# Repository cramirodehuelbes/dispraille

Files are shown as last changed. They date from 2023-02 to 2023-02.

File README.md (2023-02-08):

# Dispraille
For MakeHarvard 2023, we wanted to challenge ourselves by making a project centered around a braille display.

Dispraille is a module that uses optical character recognition (OCR) software to detect text around its user and convert it to braille using a 6-pin tactile interface. By placing a finger on the 3x2 matrix on the top of Dispraille, users can choose to read the text around them through a quick letter-by-letter run-through. For extra challenge, we chose to limit ourselves in making this project with only the materials that MakeHarvard provided, leading us to both enter in and win the top prize in the MakeHarvard Original category.

## Mechanical System
Our mechanical system used a rack and pinion mechanism to lift the pins out of the display. Since braille is very size-specific, we added bent pins in order to bypass the limitation of the larger servo motors and make the display regulation braille size with six micro-servos. We then mounted these into a custom 3D printed case and cover.

## Software
Our software system uses the OpenCV and Tesseract Python libraries in order to create a real-time optical character recognition (OCR) system. This reads text from a webcam live feed and sends serial information to an Arduino sketch, which converts the text into servo commands and lifts the corresponding pins. 

## Electrical
Our electrical subsystem is made up of an Arduino module which is connected to a Raspberry Pi through USB and our set of six motors through its six digital pins. Each pin is mapped to a different position on the braille display, and each letter is mapped to a different combination of pins according to Braille 1. Our electrical subsystem also includes a vibrating motor and a button. The vibrating motor is to alert the user that the webcam is recognizing text, while the button confirms that the user would like the text to be translated to braille.

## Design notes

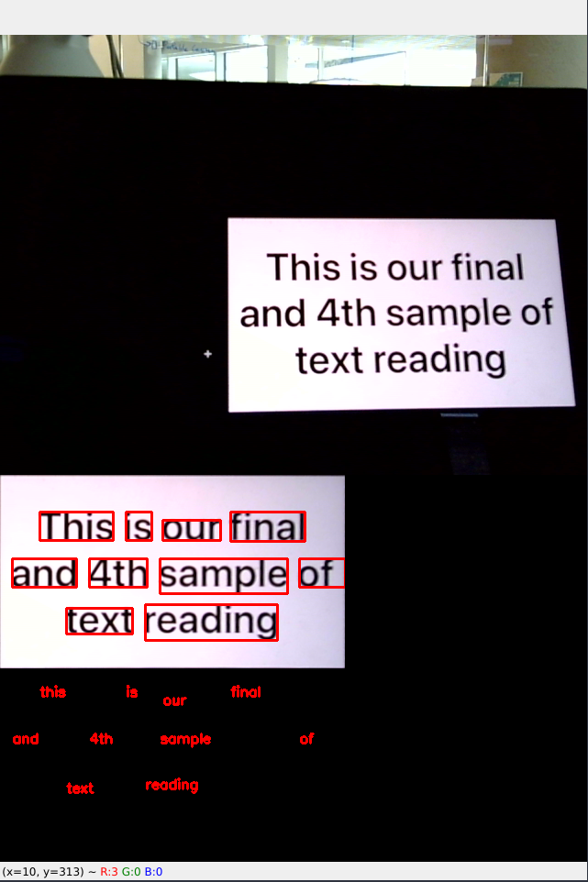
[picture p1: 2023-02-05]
vis_ss.png

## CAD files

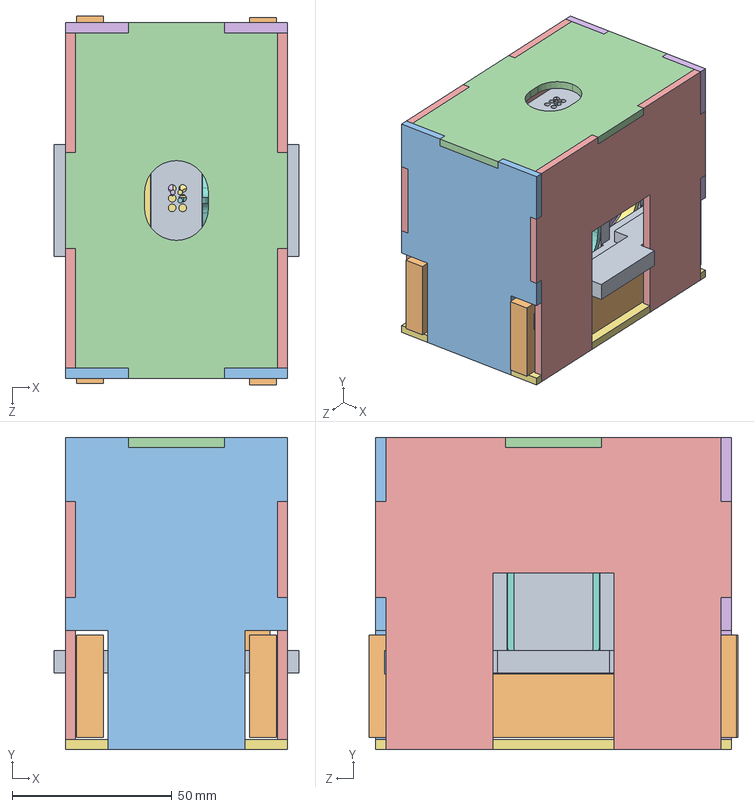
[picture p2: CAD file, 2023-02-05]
cad/Sprint 2 - x6/x6Assembly.SLDASM
76.6 x 97.7 x 115.4 mm
SixBasePart
ServoMotor
spur gear_am
rack spur rectangular_am
loop
loopArmA
loopArmB
loopArmC
Top Cover
Feet x 2
BoxBackFront
BoxRoof
BoxSides x 2
BoxBack
Box Base

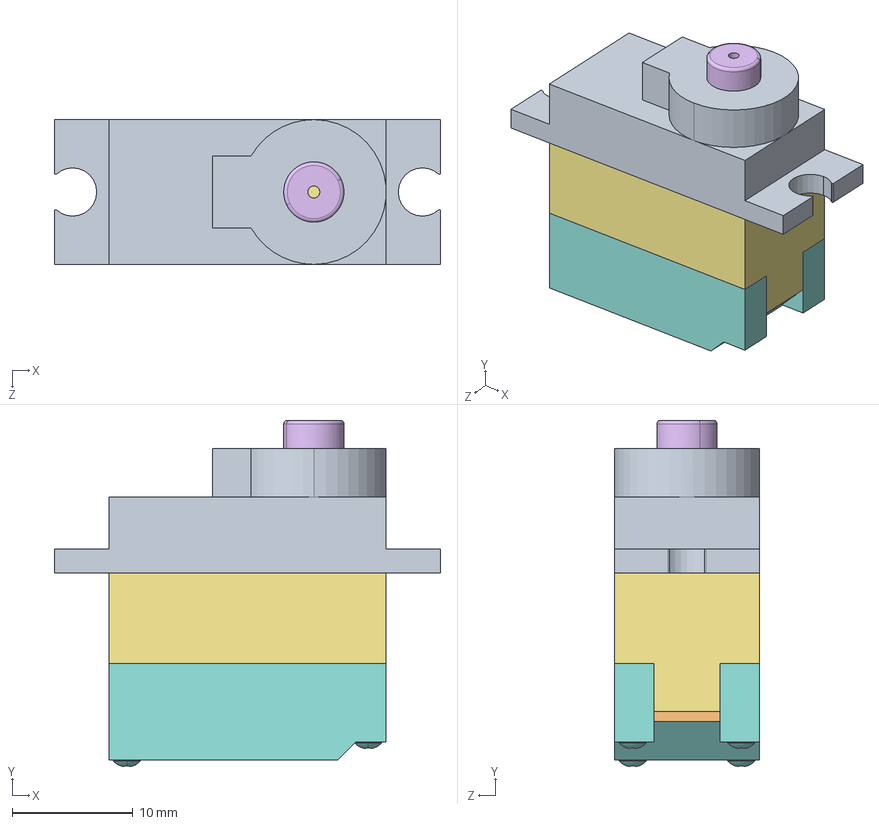
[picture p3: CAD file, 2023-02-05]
cad/Sprint 1 - RP test/ServoMotor.STEP.SLDASM
32.0 x 28.7 x 12.0 mm
spur gear_din_DIN - Spur gear 0.2M 47T 20PA 1FW ---S47A75H50L1N.STEP x 2
spur gear_din_DIN - Spur gear 0.22M 11T 20PA 1FW ---S11A75H50L1N.STEP x 2
spur gear_din_DIN - Spur gear 0.22M 42T 20PA 1FW ---S42A75H50L1N.STEP
spur gear_din_DIN - Spur gear 0.3M 10T 20PA 3FW ---S10A75H50L1N.STEP
spur gear_din_DIN - Spur gear 0.3M 28T 20PA 4FW ---S28A75H50L1N.STEP
Part1^GearC.STEP
Servo Body.STEP
Servo Bottom.STEP
Servo Top.STEP
Motor.STEP
spur gear_din_DIN - Spur gear 0.25M 10T 20PA 1FW ---S10A75H50L0.5N.STEP
Potmeter.STEP
Electronics^ServoMotor.STEP
Tengely^ServoMotor.STEP
PotiTengely^ServoMotor.STEP
cross recessed truss head screw_jis_JIS B 1111 Truss head screw M2 x 20 --8N.STEP x 4

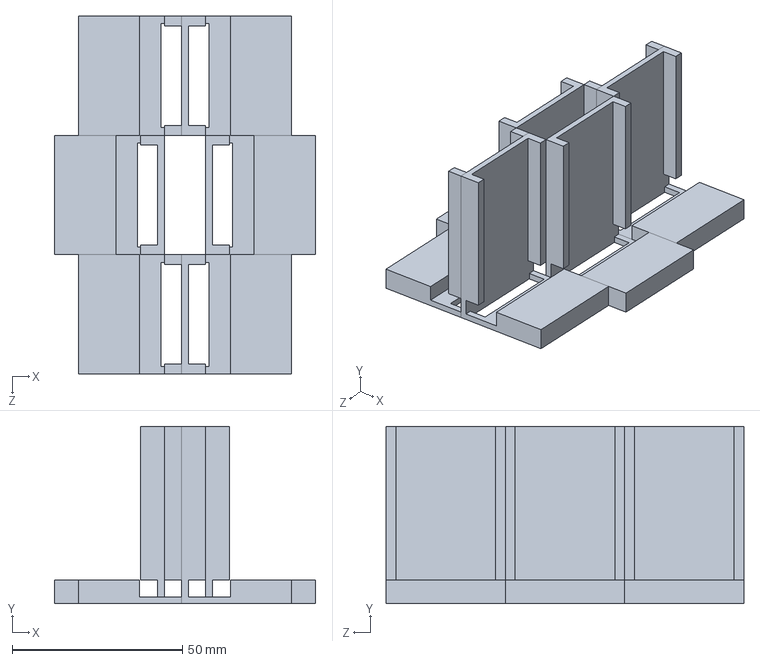
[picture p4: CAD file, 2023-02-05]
cad/Sprint 2 - x6/SixBase.SLDASM
76.6 x 52.0 x 105.0 mm
TestingRig x 6

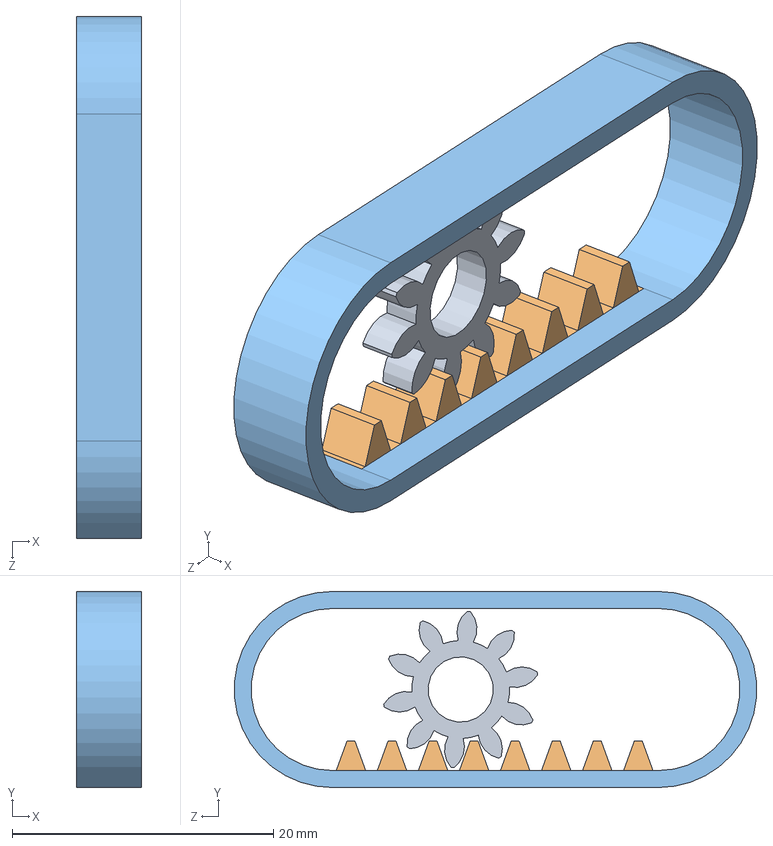
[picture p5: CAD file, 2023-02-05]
cad/Sprint 1 - RP test/RPTest0.SLDASM
5.00 x 15.0 x 39.9 mm
spur gear_am
rack spur rectangular_am
loop

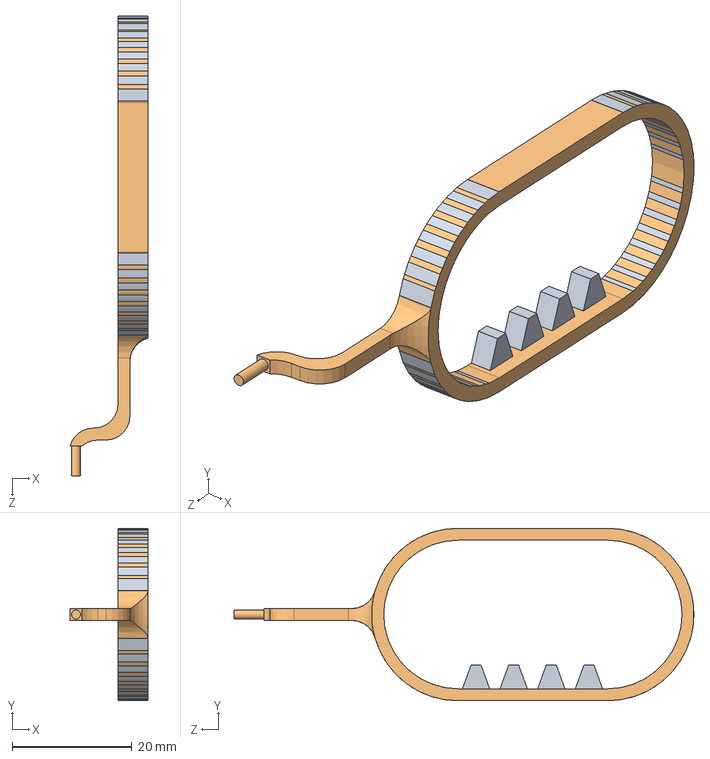
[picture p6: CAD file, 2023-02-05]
cad/Sprint 2 - x6/LoopArmTeethC.SLDASM
13.0 x 28.8 x 76.8 mm
RPTest1
loopArmC

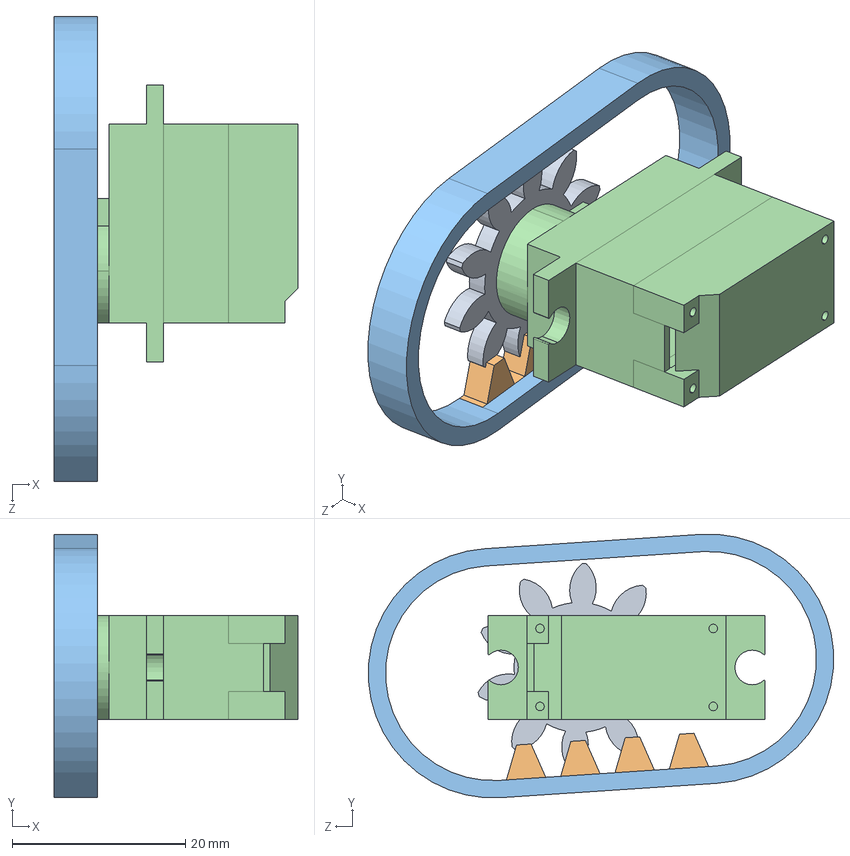
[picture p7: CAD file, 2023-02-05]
cad/Sprint 2 - x6/RPServoAssy.SLDASM
28.1 x 30.4 x 53.7 mm
spur gear_am
rack spur rectangular_am
loop
ServoMotor

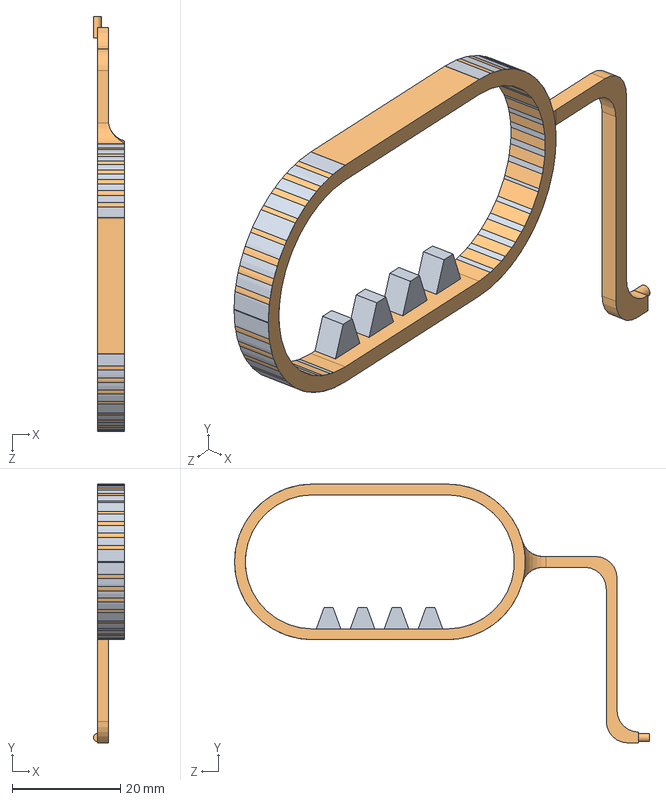
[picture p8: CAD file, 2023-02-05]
cad/Sprint 2 - x6/LoopArmTeethA.SLDASM
5.75 x 47.9 x 76.8 mm
RPTest1
loopArmA

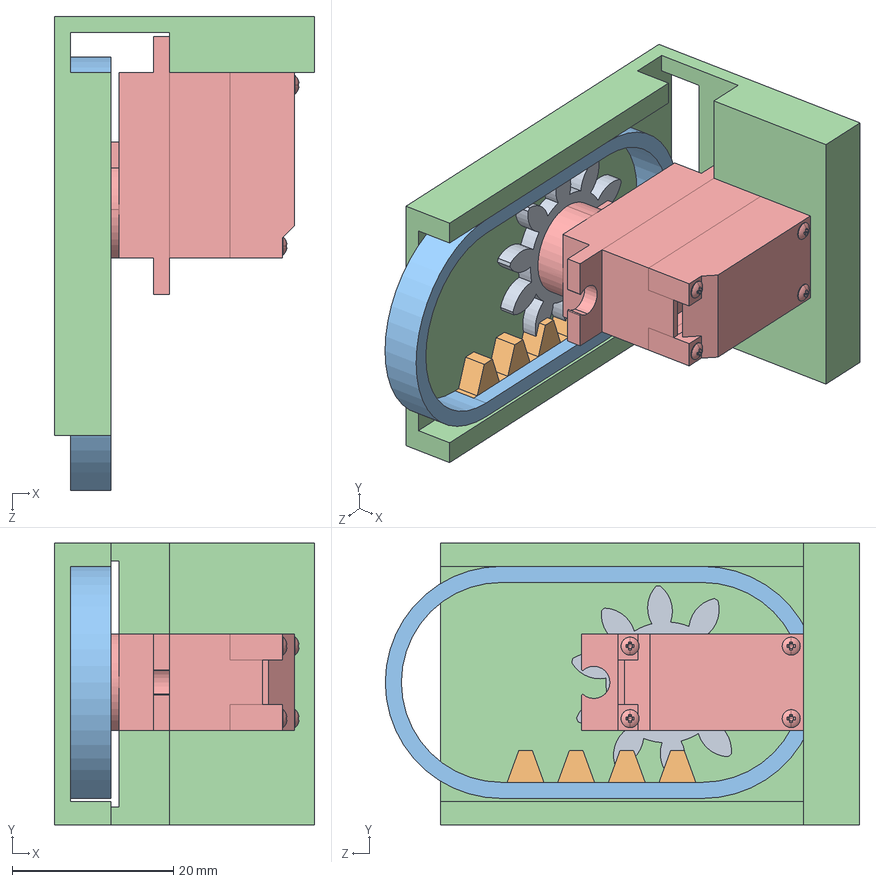
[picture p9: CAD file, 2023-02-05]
cad/Sprint 1 - RP test/RPTest1.SLDASM
32.3 x 35.0 x 58.9 mm
spur gear_am1
rack spur rectangular_am
loop
TestingRig
ServoMotor

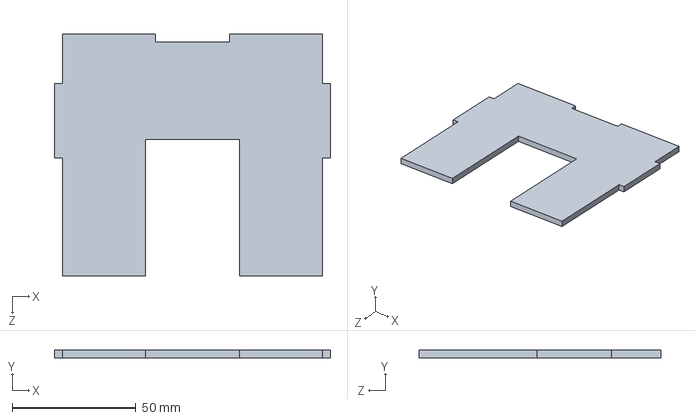
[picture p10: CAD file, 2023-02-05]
cad/BoxSides.SLDPRT
111.3 x 3.17 x 97.7 mm

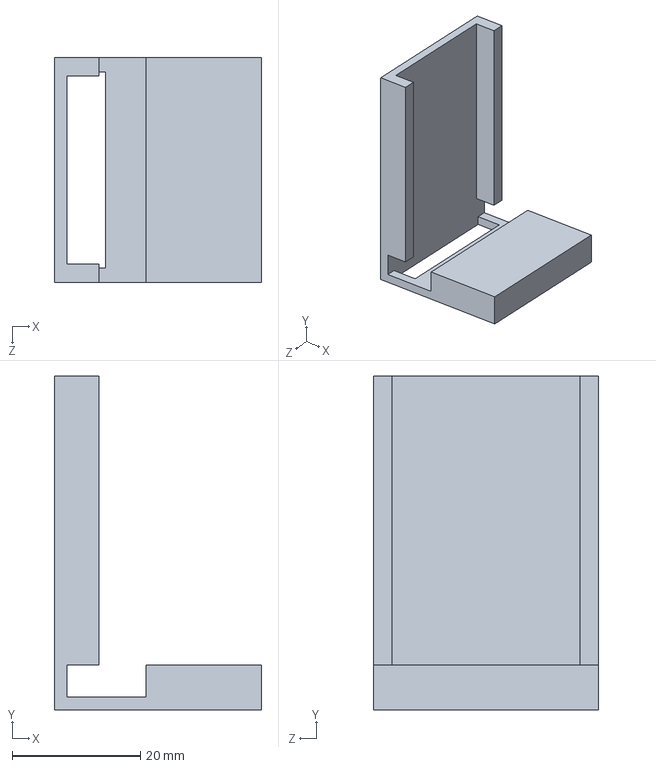
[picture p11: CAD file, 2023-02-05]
cad/Sprint 1 - RP test/TestingRig.SLDPRT
32.3 x 52.0 x 35.0 mm

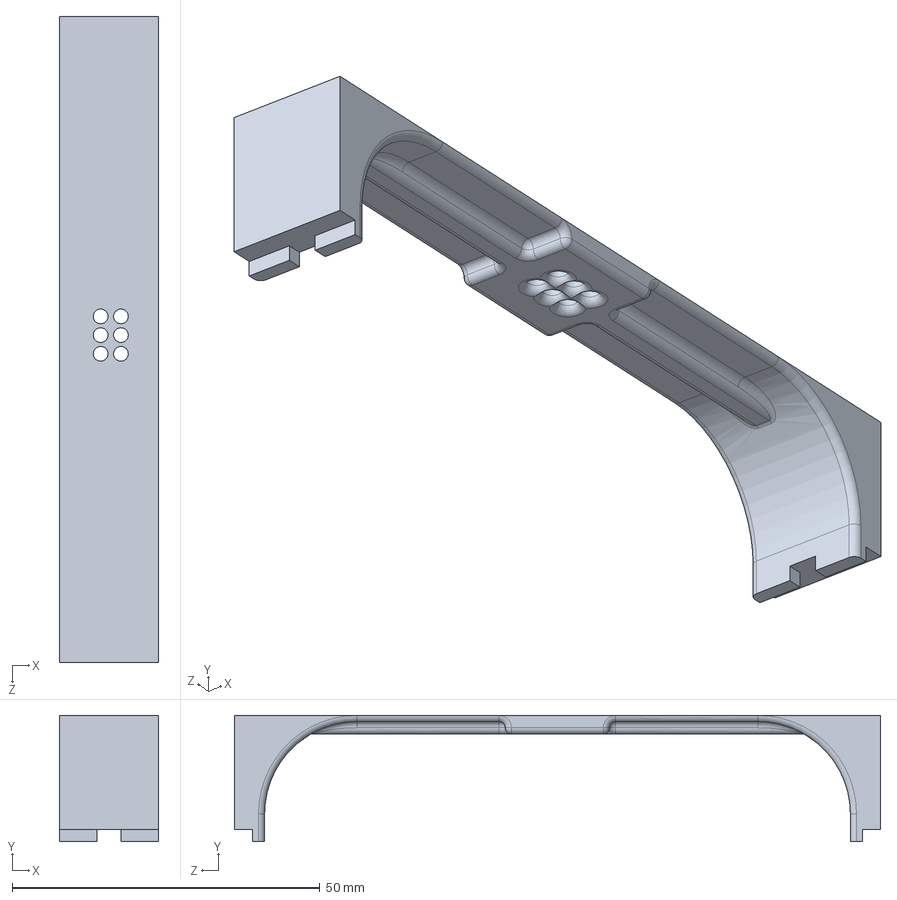
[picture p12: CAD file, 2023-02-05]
cad/Sprint 2 - x6/Top Cover.SLDPRT
16.1 x 20.5 x 105.0 mm

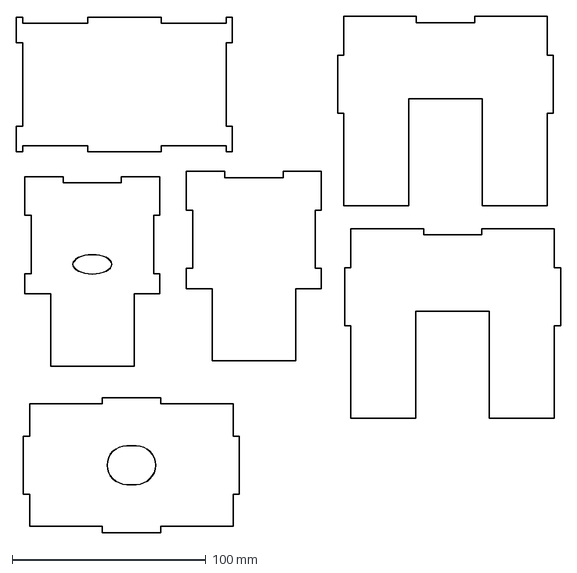
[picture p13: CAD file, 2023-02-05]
cad/Sprint 3 - packaging/CutSheetBox.DXF
280.6 x 266.2 mm

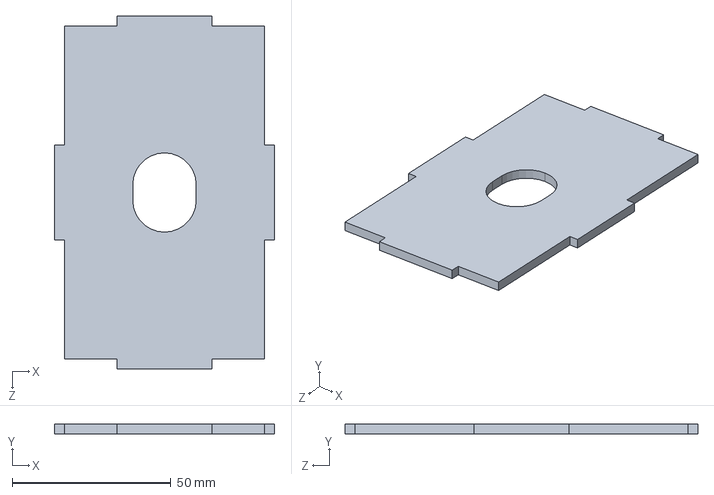
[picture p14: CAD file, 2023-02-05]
cad/BoxRoof.SLDPRT
69.6 x 3.17 x 111.4 mm

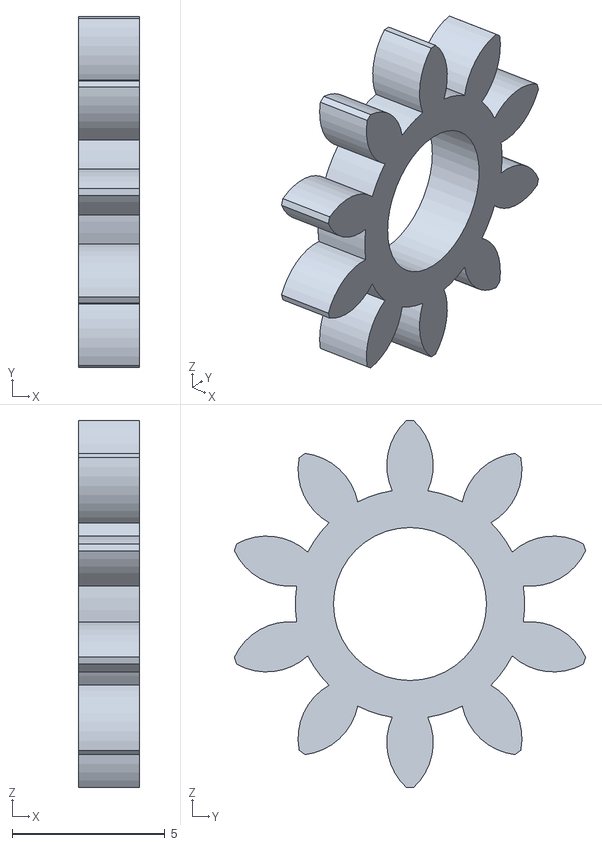
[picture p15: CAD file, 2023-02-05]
cad/Sprint 1 - RP test/spur gear_am_Test0.STL
2.00 x 11.5 x 12.0

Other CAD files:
cad/BoxBackFront.SLDPRT
cad/Sprint 2 - x6/Feet.SLDPRT
cad/Box Base.SLDPRT
cad/Sprint 1 - RP test/loop.SLDPRT
cad/BoxBack.SLDPRT
cad/ServoMotor.STEP
cad/Sprint 1 - RP test/RPTest0Copy.SLDPRT
cad/Sprint 1 - RP test/RPTest0Copy.STL
cad/Sprint 1 - RP test/RPTest1.SLDPRT
cad/Sprint 1 - RP test/RPTest1Loop.STL
cad/Sprint 1 - RP test/ServoMotor.SLDPRT
cad/Sprint 1 - RP test/TestingRigTest1.STL
cad/Sprint 1 - RP test/spur gear_am_Test1.STL
cad/Sprint 2 - x6/Feet.STL
cad/Sprint 2 - x6/Feetholees.STL
cad/Sprint 2 - x6/LoopArmTeethA.SLDPRT
cad/Sprint 2 - x6/LoopArmTeethA.STL
cad/Sprint 2 - x6/LoopArmTeethB.SLDPRT
cad/Sprint 2 - x6/LoopArmTeethB.STL
cad/Sprint 2 - x6/LoopArmTeethC.SLDPRT
cad/Sprint 2 - x6/LoopArmTeethC.STL
cad/Sprint 2 - x6/SixBasePart.SLDPRT
cad/Sprint 2 - x6/SixBasePart.STL
cad/Sprint 2 - x6/SixBasePartBraille.STL
cad/Sprint 2 - x6/Top Cover.STL
cad/Sprint 2 - x6/loopArmA.SLDPRT
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

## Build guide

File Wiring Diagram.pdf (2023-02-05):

# Enclosure

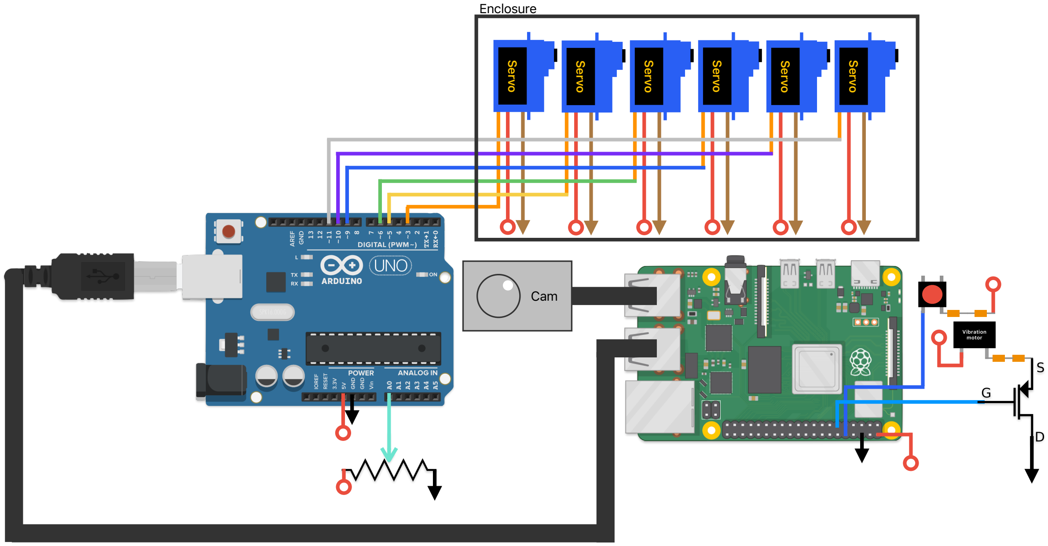
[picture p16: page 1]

# Servo

# Servo

# Servo

# Servo

Vibration
motor

# Servo

# Servo

# Cam

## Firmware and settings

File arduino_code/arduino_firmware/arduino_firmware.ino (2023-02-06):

#include <Servo.h>

#define A 0
#define B 1
#define C 2
#define D 3
#define E 4
#define F 5
#define G 6
#define H 7
#define I 8
#define J 9
#define K 10
#define L 11
#define M 12
#define N 13
#define O 14
#define P 15
#define Q 16
#define R 17
#define S 18
#define T 19
#define U 20
#define V 21
#define W 22
#define X 23
#define Y 24
#define Z 25
#define HASH 26
#define ZERO 27
#define ONE 28
#define TWO 29
#define THREE 30
#define FOUR 31
#define FIVE 32
#define SIX 33
#define SEVEN 34
#define EIGHT 35
#define NINE 36
#define SPACE 37

// create six servos
// 1  4
// 2  5
// 3  6

Servo s1;
Servo s2;
Servo s3;
Servo s4;
Servo s5;
Servo s6;


int pos = 0; // variable to store the servo position
String text; // variable to store the transmitted text
int letter;  // variable to store the current letter being displayed
int potPin = A0;   // select the input pin for the potentiometer


byte BRAILLE[][6] = {{1}, {1,2}, {1,4}, {1,4,5}, {1,5}, {1,2,4}, {1,2,4,5}, {1,2,5}, {2,4}, 
  {2,4,5}, {1,3}, {1,2,3}, {1,3,4}, {1,3,4,5}, {1,3,5}, {1,2,3,4}, {1,2,3,4,5}, {1,2,3,5}, 
  {2,3,4}, {2,3,4,5}, {1,3,6}, {1,2,3,6}, {2,4,5,6}, {1,3,4,6}, {1,3,4,5,6}, {1,3,5,6}, {3,4,5,6}, 
  {2,4}, {1}, {1,2}, {1,4}, {1,4,5}, {1,5}, {1,2,4}, {1,2,4,5}, {1,2,5}, {2,4,5} , {}};

Servo motors[6] = {s1, s2, s3, s4, s5, s6};

// servo params
int starts[] = {92, 3, 64, 71, 65, 87};
int ends[] = {74, 21, 46, 53, 83, 69};

void setup() {
  s1.attach(3);  // attaches servo pins to servo objects
  s1.write(starts[0]);
  delay(15);

  s2.attach(5);
  s2.write(starts[1]);
  delay(15);

  s3.attach(6);
  s3.write(starts[2]);
  delay(15);

  s4.attach(9);
  s4.write(starts[3]);
  delay(15);

  s5.attach(10);
  s5.write(starts[4]);
  delay(15);

  s6.attach(11);
  s6.write(starts[5]);
  delay(15);

  Serial.begin(9600);
}

void loop() {
  s1.write(starts[0]);
  delay(15);

  s2.write(starts[1]);
  delay(15);

  s3.write(starts[2]);
  delay(15);

  s4.write(starts[3]);
  delay(15);

  s5.write(starts[4]);
  delay(15);

  s6.write(starts[5]);
  delay(15);
  // Serial.println("Waiting for text to translate");

  while (Serial.available() == 0) {
 }

  text = Serial.readString(); // Read incoming data as string 
  text.toLowerCase();
  // Serial.println(text); // Print data we just read as a check

  for (int ind = 0; ind < text.length(); ind += 1){
    // Serial.println(text[ind]);
    int asciiVal = int(text[ind]);
    switch (asciiVal){
      case 97 ... 122:
        letter = asciiVal - 97 + A;
        break;
      case 48 ... 57:
        letter = asciiVal - 48 + ZERO;
        break;
      case 35:
        letter = HASH;
        break;
      default:
        letter = SPACE;
        break;
    }

    for (int i = 0; i <= sizeof(BRAILLE[letter]); i += 1) {
      // in steps of 1 degree
      motors[BRAILLE[letter][i] - 1].write(ends[BRAILLE[letter][i] - 1]);  // // tell servo to yeet to end position
      delay(15);                                  // waits 15ms for the servo to reach the position
    }                                             //}

    delay(analogRead(potPin) * 1.5 + 500);

    for (int i = 0; i <= sizeof(BRAILLE[letter]); i += 1) {
      // in steps of 1 degree
      motors[BRAILLE[letter][i] - 1].write(starts[BRAILLE[letter][i] - 1]);  // tell servo to yeet back to start position
      delay(15);                                    // waits 15ms for the servo to reach the position
    }   
  }    

  Serial.println("DONE");                                        
}

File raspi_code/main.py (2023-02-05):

import numpy as np
import cv2
import pytesseract
from pytesseract import Output
import imutils
from imutils.perspective import four_point_transform
from imutils.object_detection import non_max_suppression
import logging
import time
from cleantext import clean
from collections import Counter
import RPi.GPIO as GPIO
import re
import serial

vis = True
# Pin Setup (pins are placeholders)
VIBRATION_PIN = 17 
BUTTON_PIN = 15
GPIO.setwarnings(False)

GPIO.setmode(GPIO.BCM)
GPIO.setup(VIBRATION_PIN, GPIO.OUT)
GPIO.setup(BUTTON_PIN, GPIO.IN, pull_up_down=GPIO.PUD_DOWN)

# Serial Setup
SERIAL_RATE = 9600
try:
    ser = serial.Serial('/dev/ttyACM0', SERIAL_RATE, timeout=None)
except Exception:
    ser = serial.Serial('/dev/ttyACM1', SERIAL_RATE, timeout=None)
    
ser.reset_input_buffer()

def main():
    video = cv2.VideoCapture(0)
    logging.basicConfig(filename='playground.log', level=logging.DEBUG)
    phrases = LRUList(60)

    starttime = time.time()
    while True:
        output = None
        ret, orig = video.read()
        frame = imutils.resize(orig, width=600)
        ratio = orig.shape[1] / float(frame.shape[1])

        if cv2.waitKey(1) & 0xFF == ord('q'):
            break
        
        gray = cv2.cvtColor(frame, cv2.COLOR_BGR2GRAY)

        blurred = cv2.GaussianBlur(gray, (5, 5), 0)
        edged = cv2.Canny(blurred, 20, 100)
        cnts = cv2.findContours(edged.copy(), cv2.RETR_EXTERNAL, cv2.CHAIN_APPROX_SIMPLE)
        cnts = imutils.grab_contours(cnts)
        cnts = sorted(cnts, key=cv2.contourArea, reverse=True)[:5]

        cardCnt = None
        for c in cnts:
            peri = cv2.arcLength(c, True)
            approx = cv2.approxPolyDP(c, 0.02 * peri, True)

            if len(approx) == 4:
                cardCnt = approx
                break

        if cardCnt is not None:
            # cv2.drawContours(orig, [cardCnt], -1, (0, 255, 0), 2)
            warped = four_point_transform(orig, cardCnt.reshape(4, 2) * ratio)

            ocr = np.zeros(warped.shape, dtype="uint8")
            rgb = cv2.cvtColor(warped, cv2.COLOR_BGR2RGB)
            results = pytesseract.image_to_data(rgb, output_type=Output.DICT)
            phrase = []

            for i in range(0, len(results["text"])):
                x = results["left"][i]
                y = results["top"][i]
                w = results["width"][i]
                h = results["height"][i]

                word  = results["text"][i]
                conf = int(results["conf"][i])
                phrase.append(word)

                if conf > 20:
                    # clean text
                    word = clean(word)
                    if len(word) > 0:
                        pass
                        cv2.rectangle(warped, (x, y), (x + w, y + h), (0, 0, 255), 2)
                        cv2.putText(ocr, word, (x, y - 10), cv2.FONT_HERSHEY_SIMPLEX, 0.5, (0, 0, 255), 2)

            phrases.add(tuple(phrase))
            if vis:
                output = build_output(orig, warped, ocr)

        if vis:
            if output is not None:
                cv2.imshow("Output", output)
            else:
                cv2.imshow("Output", orig)

        try:
            mode = Counter(phrases.items).most_common(1)[0]
            print(mode)
            if mode[1] > 3 and len(mode[0]) > 3:
                vibrate_on()
                if button_pressed():
                    print('button pressed')
                    vibrate_off()
                    transmit(mode[0])
            else:
                vibrate_off()
                
        except:
            pass

        time.sleep(1/2 - ((time.time() - starttime) % 1/2))
            

    video.release()
    cv2.destroyAllWindows()
    ser.close()

def build_output(frame, warped, ocr):
    frameH, frameW = frame.shape[:2]
    cardH, cardW = (0,0)
    ocrH, ocrW = (0,0)

    if warped is not None:
        cardH, cardW = warped.shape[:2]

    if ocr is not None:
        ocrH, ocrW = ocr.shape[:2]

    outputW = max(frameW, cardW, ocrW)
    outputH = frameH + cardH + ocrH

    output = np.zeros((outputH, outputW, 3), dtype="uint8")
    output[0:frameH, 0:frameW] = frame

    if warped is not None:
        output[frameH:frameH + cardH, 0:cardW] = warped

    if ocr is not None:
        output[frameH + cardH:frameH+cardH+ocrH, 0:ocrW] = ocr
    
    return output
    
class LRUList:
    def __init__(self, max_size):
        self.items = []
        self.max_size = max_size

    def add(self, toadd):
        if len(self.items) == self.max_size:
            self.items.pop(0)
        self.items.append(toadd)

def vibrate_on():
    GPIO.output(VIBRATION_PIN, GPIO.HIGH)
    print('vibe on')

def vibrate_off():
    GPIO.output(VIBRATION_PIN, GPIO.LOW)
    print('vibe off')
    
def button_pressed():
    print(GPIO.input(BUTTON_PIN))
    return GPIO.input(BUTTON_PIN) == 1

def transmit(phrase):
    print('transmit')
    phrase = [p for p in phrase if p != '']
    phrase = " ".join(phrase)
    phrase = re.sub(r'(\d+)', r'#\1', phrase)
    print(phrase)
    ser.write(phrase.encode('utf-8'))
    ser.flushInput()
    print(phrase)

    while ser.inWaiting() == 0:
        pass
    
    if ser.inWaiting() > 0:
        print(ser.readline())
        vibrate_on()
        time.sleep(0.5)
        vibrate_off()

if __name__ == "__main__":
    main()

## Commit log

2023-02-05 Added braille_mapping.ino which converts letter codes to servo commands
2023-02-05 touched up num to servo sketch
2023-02-05 added a string to numbers for servo movements
2023-02-05 Adding final serial message and fixing lowercase error
    [braille_mapping.ino]
2023-02-05 Wiring Diagram V2.0 inclusding Pi and Camera
2023-02-05 Fixing mistakes in wiring diagram for Pi
2023-02-05 Adding all CAD files from sprints 1 and 2
    [Feet.SLDPRT, Feet.STL, Feetholees.STL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]
2023-02-05 Added functionality to actually write letters and calibration for servo motors
2023-02-05 updated wiring diagram
2023-02-05 Final CAD update, end of sprint 2 and 3
    [Box Base.SLDPRT, BoxBack.SLDPRT, BoxBackFront.SLDPRT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]
2023-02-06 arduino firmware update
